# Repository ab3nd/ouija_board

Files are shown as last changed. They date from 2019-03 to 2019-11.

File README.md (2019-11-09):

# Ouija Board
Hardware and software plans for a ouija board that is controlled by a computer as an IO device. 

Now that this is public, I thought I ought to write up a bit more of a description of what we had hoped to do, what ended up making it into the puzzle, lessons learned, and so forth. 

The initial idea of the puzzle was that players would play some sort of word game with Spirits From Beyond. The players would enter letters by sliding the Ouija board planchette around the board, and the machinery under the board would answer back. Since the easy way to drive the planchette from under the board was a magnet, we looked at a couple of different approaches for figuring out where the magnet was on the board. 

One approach was to cover the underside of the board with magnetic field visualization film, and then look at it with a camera. This has two main drawbacks, one of them being that field visualization film is expensive, and the other is that the camera has to have enough space to see the underside of the board, an unobstructed view (so the machinery has to move out of the way), and good light. This is annoying set of constraints to deal with. 

Magnets can also be sensed with Hall Effect sensors. One idea was to put a grid of sensors under the board, and interpolate the location of the planchette from the readings of multiple sensors, another option was to just have a sensor under each letter. Having a sensor under each letter means you can lose the planchetette if it's moved to some place that isn't a letter. Having a grid of sensors of sufficient resolution to detect the planchette at any location would mean we blew the budget building a PCB the size of a Ouija board, and then yours truly went nuts hand-soldering a bunch of SOT-23 parts (or I guess we contaminate someone's oven stenciling and reflowing them). So we didn't do that. 

The final approach was that the head of the machine that moves the planchette also had a ring of sensors. When it was moving the planchette, it would raise a magnet to engage the planchette, and then move to drag the planchette around. When it was sensing user input, it would lower the magnet, so it was only sensing the planchette magnet, and then move to keep the field over the sensor ring balanced. Since it was counting steps that it made to keep the magnet centered, the system would know what letter the sensor ring was under. This approach kept the sensor PCB small, reduced the number of parts needed, and could track the planchette anywhere. 

But wait, you say. When the puzzle was in operation, the players would say the word they wanted to input, and the system would then spell it and do some wiggling between yes and no. There was no actual use of the planchette as an input device!

Using the planchette as an input device had a number of problems. One was that the system could lose the planchette due to users moving it too fast, or picking it up and putting it back down somewhere else. We could have fixed that by having the system sweep the board, but that leads into the second problem, which is that there was no feedback. If the user spelled "obliges", but were closer to the 'h' than the 'i' and the system saw "oblhges", the user wouldn't have a way to see that it hadn't picked up their input properly. If it lost the planchette and was doing a sweep to find it again, the user would have no idea what was going on, and the system would be ignoring their input. 

Also, when people are properly using a Ouija board to communicate with Spirits from Beyond, they say their questions, and the spirits answer by pushing the planchette around (or it's the ideomotor effect, or Joe (that jerk) always tries to make it spell "dongs"). Since we didn't have a good way to contact players of the Game who have passed Beyond the Veil, we used baby monitors in the room with each Ouija board, and a person listening to the baby monitor. The person was SSHed into the Raspberry PI that was running each board, and used a little script to drive the planchette around. That was why the boards sometimes spelled out things like "NATO", to try to get people to spell things out with the NATO phonetic alphabet, in cases where the word they said was unclear. So while the players were speaking to Spirits from Beyond, the spirits still had their mortal shells, and were Beyond the room divider, rather than the Veil of Death.

### Actual Implementation Information

The gantry that moved the planchette was a cheapo CNC device skellington from AliExpress, which uses an Arduino and a couple of stepper motor drivers. Two of the motors drive one axis, the other axis only has one motor. They had the somewhat weird design decision that the Arduino is powered over USB, while the stepper drivers and motors have their own, independent power supply. This makes some sense, since it means that A) the Arduino doesn't need to be protected from noise from the stepper motors, and B) the parts that would normally do A are not needed, so the whole thing is cheaper for the Chinese factory it came from. 

The Arduino was controlled over a serial-over-USB link from a Raspberry Pi running stock Raspbian. A little python script presented a user interface for a person connected to the Pi via SSH, and took care of stuff like Mastermind solving, because humans are made of fallible meat, and so cannot be trusted to do Mastermind in their heads at 2AM. 

The Python for the UI and Mastermind solving is in user_console.py and mastermind.py. The control code for the Arduino is in ouija_control.ino. They communicate using a pretty simple text-based protocol. The incomplete code for following the planchette is in sensor_track.ino. It results in some very jerky movement, and it would probably be better to do some form of vector representation of the magnet displacement and a PID loop to drive that to zero when the magnet is well-centered, as well as velocity control to have it operate smoothly, but that's Left As An Exercise For The Reader. 

### Hardware Notes

The sensors we used are AH49ENTR Hall effect sensors, SOT23-3 case size. We didn't do a lot of work to characterize sensors or anything, these are just what Ross happened to have on hand. He also had the 74hc4051 8ch analog demux that was used to communicate with the sensors. The sensor ring had 8 sensors, and the mux/demux has 8 channels, addressed with three address lines, so the total pin count going into the Arduino just fit what we had available after handling the stepper controllers, limit switches, and the servo to raise/lower the magnet. Of course, none of this got used in the final version except the limit switches. 

The limit switches allow the system to drive the planchette dragging magnet to a corner, and then count steps when moving the planchette to know where it is on the board. There are only one set of limit switches, the other end of each axis' travel is handled in software, by knowing how many steps it is to the other side of the board, and not taking steps that would move the head beyond that limit. 

The sense ring PCB design is in the sense_pcb folder in this repo. It was designed in Kicad, so between that, Python, etc. pretty much the whole thing except the servo control modules and the board they are on is open source. If you get the PCBs made, OSHPark will do a slightly more expensive job of it, while DirtyPCBs will do it cheaper and far slower. I've used both, they're both good. 

The CNC gantries that moved the magnet under the board were cut down from their orignal size. Aluminum is soft. If you want to cut it, it will smear like butter into hacksaws and abrasive wheels. The tool to use is just normal wood cutting implements, like miter saws and whatnot. 

Raspbian is pretty rough around the edges, I rant about it with a lot of swearing here:

http://gizmosmith.com/2019/08/28/raspbian-still-bad/

http://gizmosmith.com/2019/08/11/the-year-of-linux-on-the-desktop-is-ha-get-fucked/

### Measurements of Ouija board

Letters - 30mm tall by 14mm (I) - 38mm (W)

"NO" - 20mm tall by 35mm wide

"YES" - 20mm tall by 45mm wide

"GOOD BYE" - 20mm by 170mm wide

Closest approach to board edge - 25mm (bottom of "GOOD BYE")

Board thickness - 3.5mm

So the maximum radius of the sense ring is 25mm + 20mm/2 = 35mm, to be able to have the center of the actuated planchette window over the centerline of the letters closest to the edge of the board. 

The minimum diameter of the sense ring would be set by the size of the letters, and appears to be around 30-35mm, so a radius of 15-17mm. 

So the radius should be at minimum 15-17mm, and at maxium 35mm, bigger is easier to build (more PCB space), but 17mm can probably fit a ring. 

Active area is a box bounded by "YES/NO" at the top, "GOOD BYE" at the bottom, and the edges of the alphabet at the sides.
These measurements are from Sarah's board, which is the 1972 Parker/Berverly board, whereas those above are from my board, a 1960s Parker/Salem board. 

Width (outside of N to outside of Z) - 360mm
Height (top of YES/NO to bottom of GOODBYE) - 230mm

Board 295mm x 445mm (Conveniently, just inside the cutting area of my laser cutter)

These measurements are from my Ouija board, which is the older model. 

Width (outside of N to outside of Z) - 375mm
Height (top of YES/NO to bottom of GOODBYE) - 235mm

Board 295mm by 446mm

So the board size is essentially exactly the same, but the printing is a little different. The same size of plotter can work with either board, and the differences in text location can be handled by calibration. 

### Some CNC Devices to Use

A4 paper size is 210 mm × 297 mm (8.27 in × 11.7 in), so the plotters with an A4-sized area are a little too small for a traditional Ouija board. 
A3 paper is 297 mm × 420 mm (11.69 in × 16.54 in), so an A3 plotter would work. 

https://www.aliexpress.com/item/DIY-XY-Plotter-drawbot-pen-drawing-robot-machine-lettering-corexy-A4-A3-engraving-area-frame-plotter/32952725307.html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,searchweb201602_6_10065_10130_10068_10890_10547_319_10546_317_10548_10545_10696_453_10084_454_10083_10618_10307_537_536_10902_10059_10884_10887_321_322_10103,searchweb201603_16,ppcSwitch_0&algo_expid=b5854729-7ad1-4867-a162-900024d3b36f-2&algo_pvid=b5854729-7ad1-4867-a162-900024d3b36f

https://www.aliexpress.com/item/50-X-65cm-Laser-Engraving-Machine-Wood-Router-CNC-DIY-Laser-Engraver-Machine-For-Desktop-Cutting/32970303676.html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,searchweb201602_6_10065_10130_10068_10890_10547_319_10546_317_10548_10545_10696_453_10084_454_10083_10618_10307_537_536_10902_10059_10884_10887_321_322_10103,searchweb201603_16,ppcSwitch_0&algo_expid=b95455ae-6d0d-4979-8a5e-edf8464dbc0f-14&algo_pvid=b95455ae-6d0d-4979-8a5e-edf8464dbc0f

Second one is huge, could be cut down to fit under board. Very tall, though. 

### Magnet Grip

We replaced the planchette window/pointer with a cut piece of acrylic with a neodymium magnet in it, 5mm is about the max diameter for the magnet to still have it look good.

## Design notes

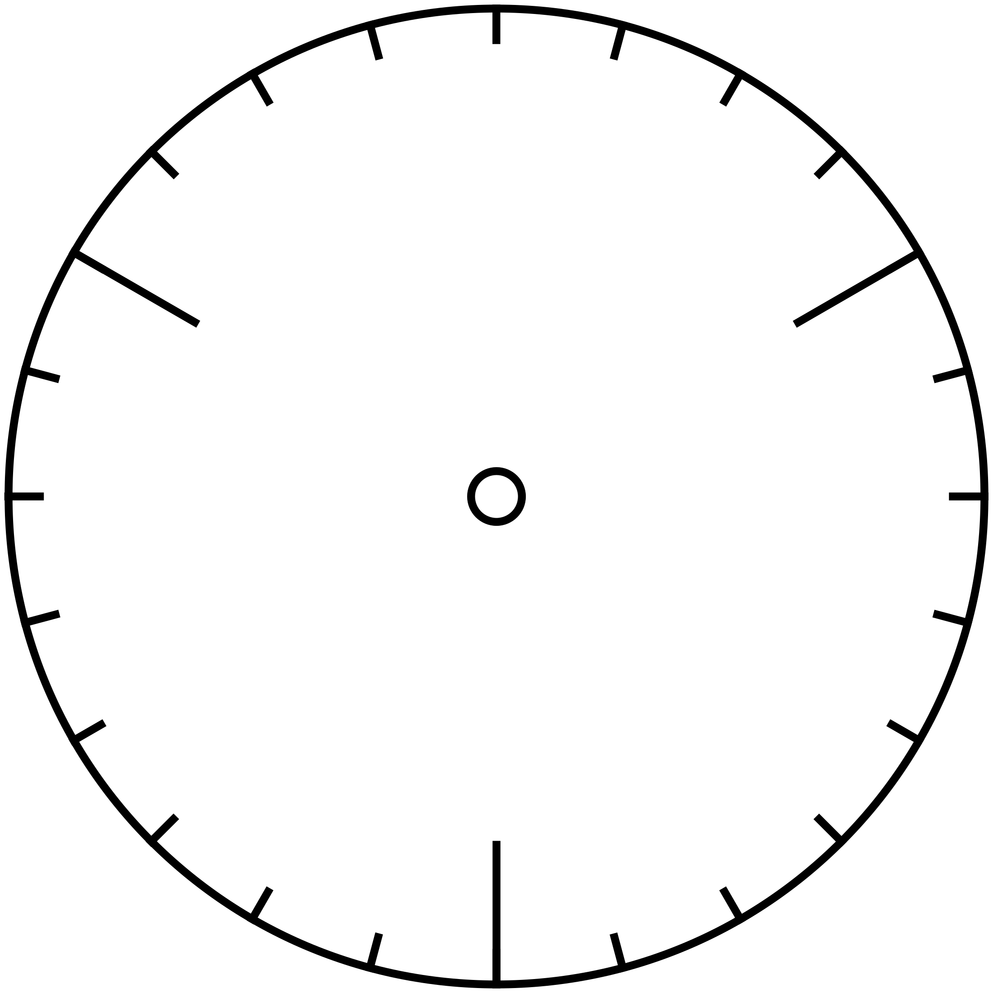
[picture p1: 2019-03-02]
graphics/layout.svg.png

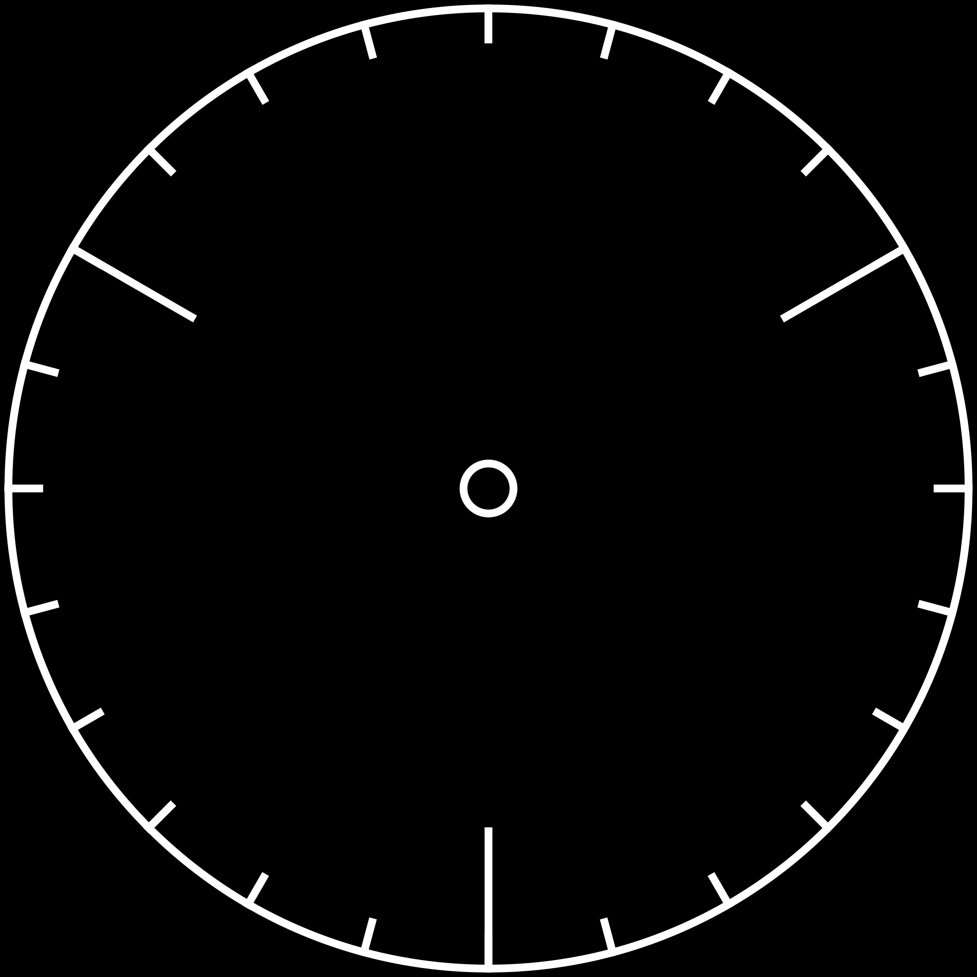
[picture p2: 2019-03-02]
graphics/layout.invert.png

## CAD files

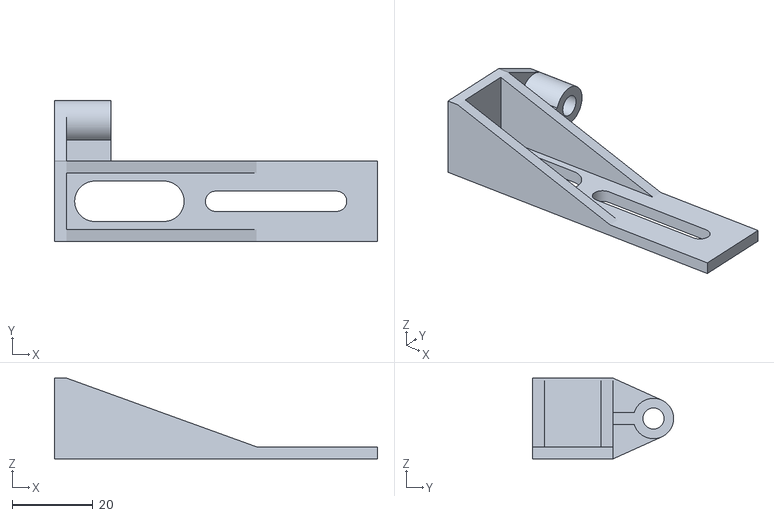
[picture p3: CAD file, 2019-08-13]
hardware/basic_magnet_holder.stl
80.0 x 35.0 x 20.0

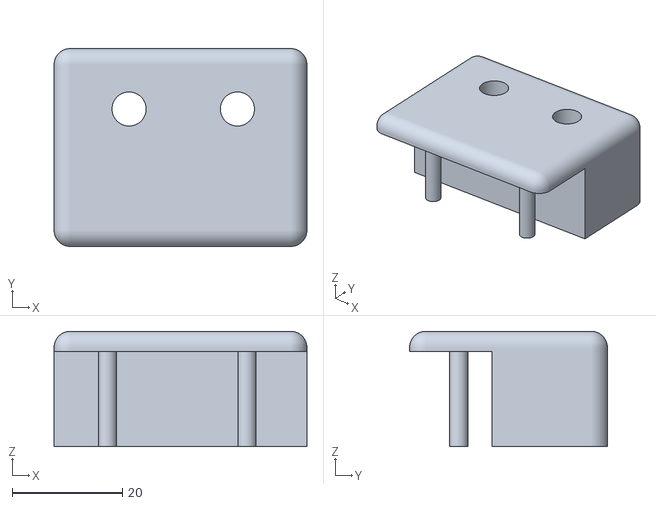
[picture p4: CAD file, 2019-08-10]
hardware/microswitch_mount.stl
46.0 x 36.0 x 21.0

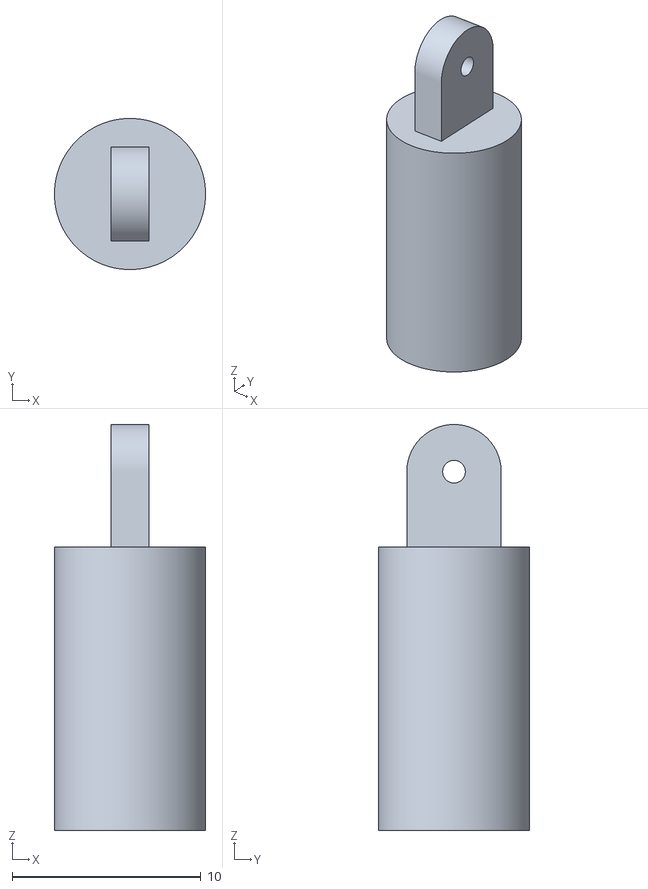
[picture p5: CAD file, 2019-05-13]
hardware/magnet_holder.stl
8.00 x 8.00 x 21.5

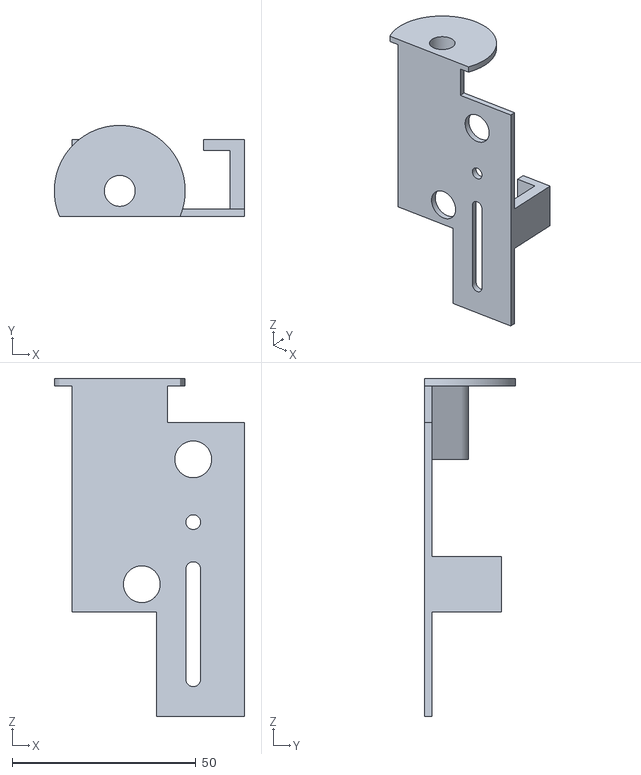
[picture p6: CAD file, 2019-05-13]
hardware/pcb_holder.stl
51.8 x 24.8 x 92.0

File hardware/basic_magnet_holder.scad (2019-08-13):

$fn=60;

module mount_surface(){
    difference(){
        union(){
            angle_length = 50;
            angle_height = 20;
            thickness = 3;
            //Flanges on the sides
            hull(){
                translate([0, 7, 0]){
                    cube([angle_length, thickness, thickness]);
                    cube([thickness, thickness, angle_height]);
                }
            }
            hull(){
                translate([0,-10, 0]){
                    cube([angle_length, thickness, thickness]);
                    cube([thickness, thickness, angle_height]);
                }
            }
            
            //Mount panel
            translate([0,-10,0]){
                cube([80,20,thickness]);
            }
            
            //Magnet
            translate([0,20,10]){
                rotate([0, 90, 0]){
                    difference(){
                        cylinder(r=5, h=14);

                    }
                }
            }
            

            
            //Rectangle connector
            translate([0,10,8.5]){
                cube([14,7,3]);
            }
            
            //Flat end connector
            hull(){
                translate([0,20,10]){
                    rotate([0, 90, 0]){
                        cylinder(r=5, h=3);
                    }
                }
                translate([0,-10, 0]){
                    cube([3, 20, angle_height]);
                }
            }
        }
        
        
        // Cutouts for mounting
        union(){
            translate([0,0,-1]){
                translate([10, 0, 0]){
                    cylinder(h=8, r=5);
                }
                
                translate([25.1+2, 0, 0]){
                    cylinder(h=8, r=5);
                }
                   
                translate([10,-5, 0]){
                    cube([17,10,8]);
                }

                translate([25.1+4+10.78, 0, 0]){
                    cylinder(h=8, r=2.5);
                    translate([0,-2.5, 0]){
                        cube([30,5,8]);
                    }
                }
                
                translate([25.1+4+10.78 +30, 0, 0]){
                    cylinder(h=8, r=2.5);
                }
            }

            //Magnet hole
            translate([0,20,10]){
                rotate([0, 90, 0]){
                    translate([0,0,-0.5]){
                        cylinder(r=2.62, h=15);
                    }
                }
            }               
         }
      }
  }




mount_surface();

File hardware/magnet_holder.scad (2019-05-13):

module magnet_holder(){
   //Body with hole
   difference(){
      cylinder(r=4, h=15, $fn=200);
      translate([0,0,-3]){
         cylinder(r=2.6, h=15, $fn=200);
      }
   }

   //Tab with a hole in it
   difference(){
      union(){
         translate([-2.5, 0, 19]){
            translate([1.5, 0, 0]){
               rotate([0,90,0]){
                  cylinder(r=2.5, h=2, $fn=200);
               }
            }
         }

         translate([0,0,17]){
               cube([2,5,4], center=true);
         }
      }

      translate([-2.5, 0, 19]){
         rotate([0,90,0]){
            cylinder(r=0.6, h=5, $fn=200);
         }
      }
   }
}

magnet_holder();

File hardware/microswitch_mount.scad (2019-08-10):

$fn = 60;

module microswitch(){
    sw_hole_d = 3.3;
    sw_hole_r = sw_hole_d/2;
    sw_hole_h = 4 + sw_hole_r+0.4;
    sw_hole_offset = 9.7 + sw_hole_r+0.4;
    sw_hole_sep = 25.35;

    difference(){
        //Body of the microwitch
        color("grey"){
            cube([49.2, 17.3, 20.9]);
        }

        //Mount holes
        translate([sw_hole_offset, -1, sw_hole_h]){ 
            rotate([-90,0,0]){
                cylinder(r = sw_hole_r, h = 25);
                translate([sw_hole_sep, 0, 0]){
                    cylinder(r=sw_hole_r, h = 25);
                }
            }
        }
    }
}

module holder(){
    difference(){
        translate([5, -12, 0]){ 
            color("blue"){
                minkowski(){
                    cube([40, 30, 18]);
                    sphere(r=3);
                }
            }
        }
        
        //measured from the strut
        groove_w = 6.2;
        translate([25.5, 10, -10]){
            translate([(13.5+groove_w)/2, 0, 0]){
                cylinder(r=groove_w/2, h = 40);
            }
            translate([-(13.5+groove_w)/2, 0, 0]){
                cylinder(r=groove_w/2, h = 40);
           }
        }
        
        //Delete the bottom face
        translate([0,-20,-7.9999]){
            cube([50, 50, 8]);
        }
    }
}

difference(){
    holder();
    rotate([90, 0, 0]){
        microswitch();
    }
}

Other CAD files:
hardware/pcb_holder.scad

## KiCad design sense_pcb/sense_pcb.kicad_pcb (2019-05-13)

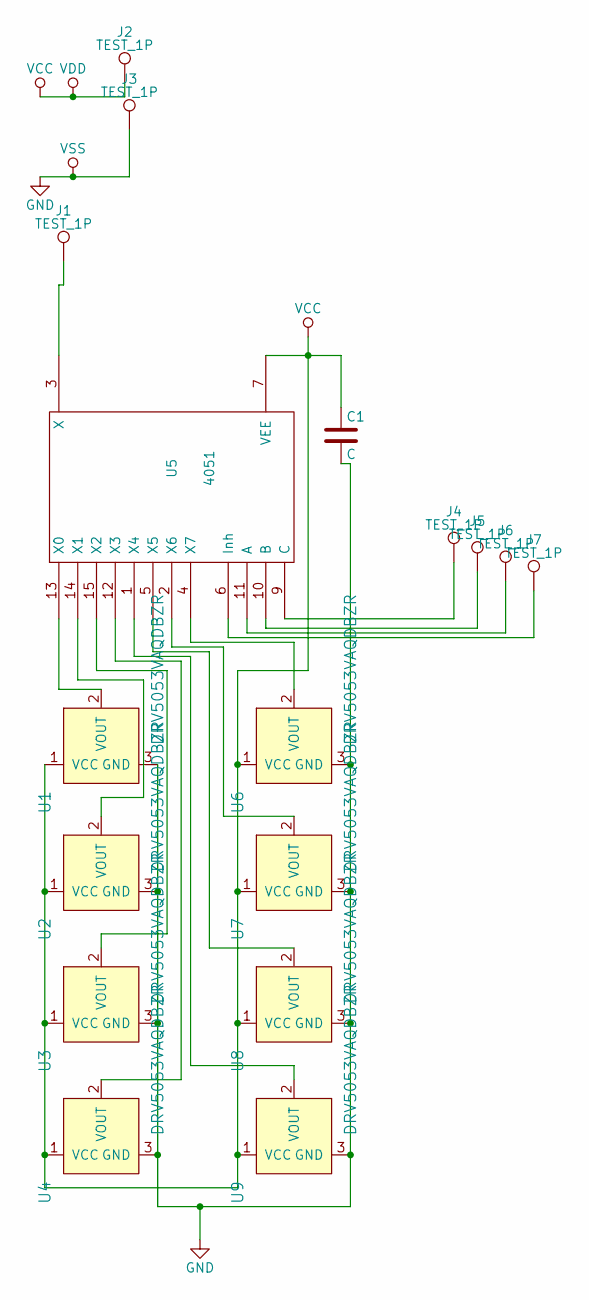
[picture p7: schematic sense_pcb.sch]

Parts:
C1: C; C_1206_HandSoldering
J1, J2, J3, J4, J5, J6, J7: TEST_1P; Measurement_Point_Round-SMD-Pad_Small
U1, U2, U3, U4, U6, U7, U8, U9: DRV5053VAQDBZR; SOT-23-3; MPN DRV5053VAQDBZR; Digi-Key_PN 296-38460-1-ND
U5: 4051; SO-16-N

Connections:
GND: C1.2, J3.1, U1.3 (GND), U2.3 (GND), U3.3 (GND), U4.3 (GND), U5.8 (VSS), U6.3 (GND), U7.3 (GND), U8.3 (GND), U9.3 (GND)
unnamed: J1.1, U5.3 (X)
unnamed: J4.1, U5.9 (C)
unnamed: J5.1, U5.10 (B)
unnamed: J6.1, U5.11 (A)
unnamed: J7.1, U5.6 (Inh)
unnamed: U1.2 (VOUT), U5.13 (X0)
unnamed: U2.2 (VOUT), U5.14 (X1)
unnamed: U3.2 (VOUT), U5.15 (X2)
unnamed: U4.2 (VOUT), U5.12 (X3)
unnamed: U5.1 (X4), U9.2 (VOUT)
unnamed: U5.2 (X6), U7.2 (VOUT)
unnamed: U5.4 (X7), U6.2 (VOUT)
unnamed: U5.5 (X5), U8.2 (VOUT)
VCC: C1.1, J2.1, U1.1 (VCC), U2.1 (VCC), U3.1 (VCC), U4.1 (VCC), U5.7 (VEE), U5.16 (VDD), U6.1 (VCC), U7.1 (VCC), U8.1 (VCC), U9.1 (VCC)

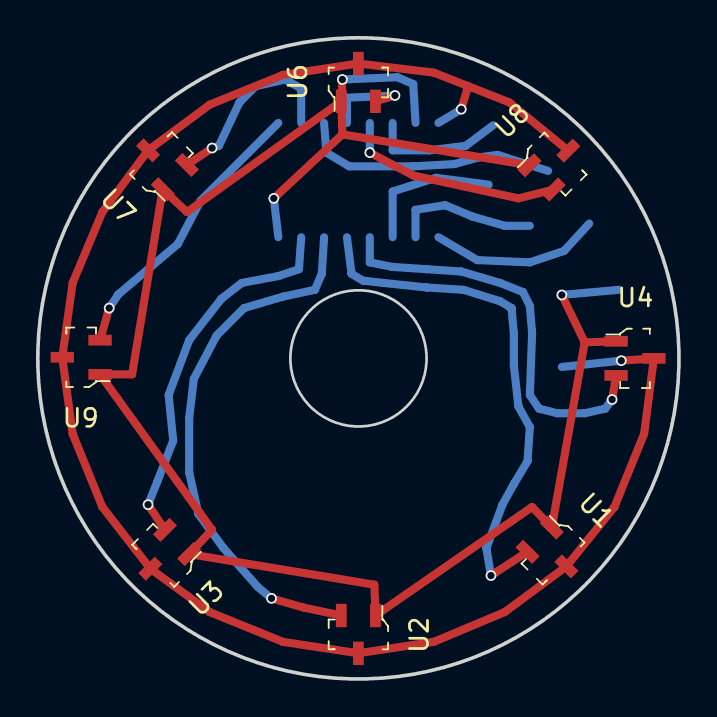
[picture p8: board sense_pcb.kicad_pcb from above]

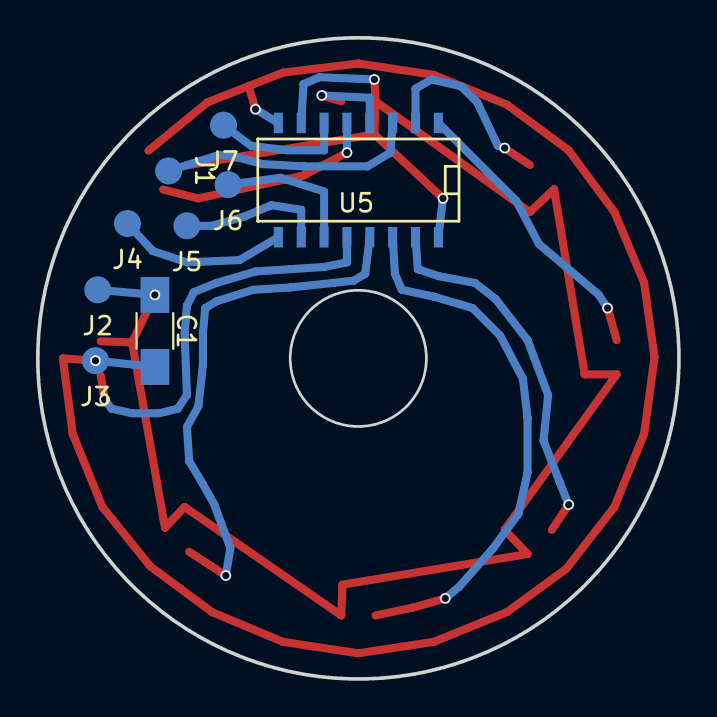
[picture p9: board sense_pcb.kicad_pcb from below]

Board: 2 copper layers, 35.6 x 35.6 mm, 17 parts (9 on the bottom side), 15 nets.

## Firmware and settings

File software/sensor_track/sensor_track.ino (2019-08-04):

/* Control software for the Ouija Board. The board is an Arduino Nano with the old bootloader.
   By Ab3nd.
*/

#include <Servo.h>

//Limit switch connections
#define LIMIT_X 9
#define LIMIT_Y 10

//Stepper control
#define ENABLE 8
#define DIR_X 5
#define DIR_Y 6
#define STEP_X 2
#define STEP_Y 3

//Sensor
#define ENABLE_SENSE 4
#define S0 7
#define S1 11
#define S2 12
#define SENSE A0

#define SERVO_PIN 13

//Measurements, from home, of the working area, in steps
#define Y_MAX 30921
#define X_MAX 18995

/* "NO"   600   5500
   "YES"  600   24600
   A      8800  29000
   B      7200  26500
   C      6500  24000
   D      5500  22000
   E      5200  20000
   F      5100  17500
   G      5000  15500
   H      5000  13500
   I      5000  11000
   J      5500  9000
   K      6000  7000
   L      6800  4500
   M      8300  2300
   N      13200 28300
   O      11600 26400
   P      10600 24400
   Q      9600  22400
   R      8800  20200
   S      8600  17700
   T      8400  15700
   U      8100  13500
   V      8300  11000
   W      9000  8500
   X      10500 6100
   Y      11500 4000
   Z      12800 1800
*/
int current_x = 0;
int current_y = 0;

struct point {
  int x;
  int y;
};

//26 letters, in order a-z
struct point letters[26] = {
  {8800, 29000},
  {7200, 26500},
  {6500, 24000},
  {5500, 22000},
  {5200, 20000},
  {5100, 17500},
  {5000, 15500},
  {5000, 13500},
  {5000, 11000},
  {5500, 9000},
  {6000, 7000},
  {6800, 4500},
  {8300, 2300},
  {13200, 28300},
  {11600, 26400},
  {10600, 24400},
  {9600, 22400},
  {8800, 20200},
  {8600, 17700},
  {8400, 15700},
  {8100, 13500},
  {8300, 11000},
  {9000, 8500},
  {10500, 6100},
  {11500, 4000},
  {12800, 1800}
};

point no = {600, 5500};
point yes = {600, 24600};

int readings[8] = {0, 0, 0, 0, 0, 0, 0, 0};
int cal_readings[8] = {0, 0, 0, 0, 0, 0, 0, 0};

/* Map counts on the address lines of the mux to indices for readings
   so that the readings are sequential around the ring */
int addr_map[8] = {0, 1, 2, 7, 3, 6, 4, 5};

Servo mag_lift;

String serial_cmd;
String guess;

//The time in millis the system last moved
unsigned long last_moved;

//The last character the system sent
char last_sent;

bool sent_answer;
bool sent_msg;

void setup() {

  //Set up the magnet height
  mag_lift.attach(SERVO_PIN);
  //90 is very low, 40 looks about good
  mag_lift.write(40);

  //Limit switches
  pinMode(LIMIT_X, INPUT);
  pinMode(LIMIT_Y, INPUT);

  //Set up the stepper control
  pinMode(ENABLE, OUTPUT);
  pinMode(DIR_X, OUTPUT);
  pinMode(DIR_Y, OUTPUT);
  pinMode(STEP_X, OUTPUT);
  pinMode(STEP_Y, OUTPUT);

  // Hall ring sensor
  pinMode(ENABLE_SENSE, OUTPUT);
  pinMode(S0, OUTPUT);
  pinMode(S1, OUTPUT);
  pinMode(S2, OUTPUT);
  pinMode(SENSE, INPUT);

  // Set up sensor
  digitalWrite(ENABLE_SENSE, HIGH);
  digitalWrite(S0, LOW);
  digitalWrite(S1, LOW);
  digitalWrite(S2, LOW);

  //Accumulate 10 samples
  for (int count = 0; count < 10; count++) {
    for (byte ii = 0; ii < 8; ii++)
    {
      //Disable the switch
      digitalWrite(ENABLE_SENSE, HIGH);
      //Set the address bits
      (ii & B00000001) ? digitalWrite(S0, HIGH) : digitalWrite(S0, LOW);
      (ii & B00000010) ? digitalWrite(S1, HIGH) : digitalWrite(S1, LOW);
      (ii & B00000100) ? digitalWrite(S2, HIGH) : digitalWrite(S2, LOW);
      digitalWrite(ENABLE_SENSE, LOW);
      cal_readings[addr_map[ii]] += analogRead(SENSE);
    }
  }

  //Get their average
  for (int idx = 0; idx < 8; idx++)
  {
    //Each reading should be around 512 with no magnet, so these
    //should all be around 5120, and so not have an underflow
    //dividing by 10
    cal_readings[idx] = cal_readings[idx] / 10;
  }

  //For debugging
  Serial.begin(9600);

  //Just for initialization
  last_moved = millis();
}


void move_home() {
  //Enable stepper drivers
  digitalWrite(ENABLE, LOW);

  //Home x axis first
  digitalWrite(DIR_X, LOW);
  digitalWrite(STEP_X, LOW);
  while (digitalRead(LIMIT_X) == 1) {
    digitalWrite(STEP_X, HIGH);
    delayMicroseconds(200);
    digitalWrite(STEP_X, LOW);
    delayMicroseconds(200);
  }

  //Home Y axis, it uses opposite DIR_Y setting
  digitalWrite(DIR_Y, HIGH);
  digitalWrite(STEP_Y, LOW);
  while (digitalRead(LIMIT_Y) == 1) {
    digitalWrite(STEP_Y, HIGH);
    delayMicroseconds(200);
    digitalWrite(STEP_Y, LOW);
    delayMicroseconds(200);
  }

  //Disable stepper drivers
  digitalWrite(ENABLE, HIGH);

  //Reset the position counters
  current_x = current_y = 0;
}

void single_step(int dir, int axis, int vel) {

  // Enable axis and maintain step counts
  digitalWrite(ENABLE, LOW);
  if (axis == STEP_X) {
    digitalWrite(DIR_X, dir);
    //High is away from home for X
    if (dir) {
      current_x++;
    }
    else {
      current_x--;
    }
  }
  else {
    digitalWrite(DIR_Y, dir);
    //HIGH is towards home for Y
    if (dir) {
      current_y--;
    }
    else {
      current_y++;
    }
  }

  // Single step
  digitalWrite(axis, HIGH);
  delayMicroseconds(vel);
  digitalWrite(axis, LOW);
  delayMicroseconds(vel);

  //Update last move
  last_moved = millis();
}

void move_to(int x, int y, int vel) {
  //In this house, we only move within the operating area of the gantry
  y = constrain(y, 0, Y_MAX);
  x = constrain(x, 0, X_MAX);

  //Figure out X and Y directions
  int x_dir = HIGH;  // Away from home
  if ((current_x - x) > 0) {
    x_dir = LOW;  // Towards home
  }

  int y_dir = LOW;  //Away from home
  if ((current_y - y) > 0) {
    y_dir = HIGH;  // Towards home
  }

  //Ratio of X to Y, so how many steps to take of each per cycle
  float ratio = float(abs(current_x - x)) / float(abs(current_y - y));

  int stepX, stepY;
  if (ratio >= 1) {
    stepX = int(ratio);
    stepY = 1;
  } else {
    stepX = 1;
    stepY = int(1.0 / ratio);
  }

  while ((current_y != y) && (current_x != x)) {
    //Do the x steps, if any
    for (int ii = 0; ii < stepX; ii++) {
      if (current_x == x) {
        break;
      }
      single_step(x_dir, STEP_X, vel);
    }
    //Do the y steps, if any
    for (int ii = 0; ii < stepY; ii++) {
      if (current_y == y) {
        break;
      }
      single_step(y_dir, STEP_Y, vel);
    }
  }

  while (current_y != y) {
    single_step(y_dir, STEP_Y, vel);
  }

  while (current_x != x) {
    single_step(x_dir, STEP_X, vel);
  }
}

void say_string(String msg) {
  int index = 0;
  struct point p;
  //For all the letters
  for (int ii = 0; ii < msg.length(); ii++) {
    //String is all lowercase, so subtracting 'a' converts from ascii
    //to a=0, b=1, c=2,..., which can then be used to
    //look up coordinates in a lookup table and move
    index = msg[ii] - 'a';
    p = letters[index];
    move_to(p.x, p.y, 100);
    //Delay to let people read it off
    delay(1000);
    //If the next letter is the same as this letter
    while ((ii != msg.length() - 1) && (msg[ii] == msg[ii + 1])) {
      //Skip the next letter
      ii++;
      //move off this letter and then back on
      move_to(current_x - 800, current_y - 800, 100);
      move_to(current_x + 800, current_y + 800, 100);
      delay(1000);
    }
  }
}

void update_sensor() {
  for (byte ii = 0; ii < 8; ii++)
  {
    //Disable the switch
    digitalWrite(ENABLE_SENSE, HIGH);
    //Set the address bits
    (ii & B00000001) ? digitalWrite(S0, HIGH) : digitalWrite(S0, LOW);
    (ii & B00000010) ? digitalWrite(S1, HIGH) : digitalWrite(S1, LOW);
    (ii & B00000100) ? digitalWrite(S2, HIGH) : digitalWrite(S2, LOW);
    digitalWrite(ENABLE_SENSE, LOW);
    readings[addr_map[ii]] = analogRead(SENSE) - cal_readings[addr_map[ii]];
  }
}

bool close_to(int a, int b, int thresh) {
  return b - thresh <= a <= b + thresh;
}

float distance(point p1, point p2) {
  return sqrt(pow(p1.x - p2.x, 2) + pow(p1.y - p2.y, 2));
}

char closest_letter() {
  //Hacky, but the biggest distance between two points on the
  //board can't be more than the sum of the edges of the board
  unsigned long min_dist = X_MAX + Y_MAX;
  int min_idx = 0;
  float d = 0;
  point current = {current_x, current_y};
  for (int ii = 0; ii < 25; ii++) {
    d = distance(current, letters[ii]);
    if (d < min_dist)
    {
      min_idx = ii;
      min_dist = d;
    }
  }

  //Capital A is 65;
  char retval = (char)(min_idx + 65);

  //Check if the distance to "No" is even closer
  d = distance(no, current);
  if (d < min_dist) {
    retval = 0;
    min_dist = d;
  }
  
  //Finally, check if the distance to "Yes" is closer
  d = distance(yes, current);
  if (d < min_dist) {
    retval = 1;
    min_dist = d;
  }

  //Too far from any letter to count
  if(min_dist > 2000)
  {
    retval = 2;
  }

  //Return is a char, but it's 0 for No, 1 for Yes, 2 for no letter, and the letter for A-Z
  return retval;
}

void follow_planchette() {
  int vel = 100;
  int move_thresh = 10;

  //Get the maximum sensor reading
  byte max_idx = 0;
  int max_val = 0;
  for (byte ii = 0; ii < 8; ii++)
  {
    if (readings[ii] > max_val)
    {
      max_val = readings[ii];
      max_idx = ii;
    }
  }

  //If we need to get moving
  if (max_val > move_thresh) {
    //Get the second max
    byte second_max_idx = 0;
    byte second_max = 0;

    if (max_idx == 0)
    {
      //Handle wrap at zero
      (readings[max_idx + 1] > readings[7]) ? second_max_idx = max_idx + 1 : second_max_idx = 7;
    }
    else if (max_idx == 7)
    {
      //Handle wrap at 7
      (readings[0] > readings[max_idx - 1]) ? second_max_idx = 0 : second_max_idx = max_idx - 1;
    }
    else
    {
      //Check sensors next to this sensor
      (readings[max_idx + 1] > readings[max_idx - 1]) ? second_max_idx = max_idx + 1 : second_max_idx = max_idx - 1;
    }

    //Figure out the move
    int move_dist = 15 * max_val; //was 200
    int target_x = current_x;
    int target_y = current_y;

    //Add a little bit to current postion to get new position
    if ((max_idx == 0 && second_max_idx == 1) || (max_idx == 1 && second_max_idx == 0))
    {
      //Down and Left
      target_x += move_dist;
      target_y += move_dist;
    }
    else if ((max_idx == 1 && second_max_idx == 2) || (max_idx == 2 && second_max_idx == 1))
    {
      //Left
      target_y += move_dist;
    }
    else if ((max_idx == 2 && second_max_idx == 3) || (max_idx == 3 && second_max_idx == 2))
    {
      //Up and Left
      target_x -= move_dist;
      target_y += move_dist;
    }
    else if ((max_idx == 3 && second_max_idx == 4) || (max_idx == 4 && second_max_idx == 3))
    {
      //Up
      target_x -= move_dist;
    }
    else if ((max_idx == 4 && second_max_idx == 5) || (max_idx == 5 && second_max_idx == 4))
    {
      //Up and Right
      target_x -= move_dist;
      target_y -= move_dist;
    }
    else if ((max_idx == 5 && second_max_idx == 6) || (max_idx == 6 && second_max_idx == 5))
    {
      //Right
      target_y -= move_dist;
    }
    else if ((max_idx == 6 && second_max_idx == 7) || (max_idx == 7 && second_max_idx == 6))
    {
      //Down and Right
      target_x += move_dist;
      target_y -= move_dist;
    }
    else if ((max_idx == 7 && second_max_idx == 0) || (max_idx == 0 && second_max_idx == 7))
    {
      //Down
      target_x += move_dist;
    }

    move_to(target_x, target_y, vel);
  }
}

void move_yes() 
{
  if ((current_y == 24600) && (current_x == 600)) {
    //move off and then back on
    move_to(current_x - 500, current_y - 800, 100);
    move_to(current_x + 500, current_y + 800, 100);
  }
  else {
    move_to(600, 24600, 100);
  }  
}

void move_no()
{
  if ((current_y == 5500) && (current_x == 600)) {
    //move off and then back on
    move_to(current_x - 500, current_y - 800, 100);
    move_to(current_x + 500, current_y + 800, 100);
  }
  else {
    move_to(600, 5500, 100);
  }  
}

bool get_serial_cmd() {
  Serial.println("get_serial_cmd called");
  
  while (!Serial.available()) {} // wait for data to arrive

  int index = 0;
  
  if (Serial.available()) {
    serial_cmd = Serial.readStringUntil('\n');
    //Previous line would block until we got something
    //The returning command from the user is a string to say,
    //And then a yes/no answer string
    if (serial_cmd.startsWith("s")) {

      //Split on first space, command is of the form "s some string here"
      index = serial_cmd.indexOf(" ");
      String message = serial_cmd.substring(index + 1);
      //Send it back as confirmation
      say_string(message);

      sent_msg = true;
    }
    else if (serial_cmd.startsWith("a")) {
      //Answer, message is of the form "a yyny" or similar 
      index = serial_cmd.indexOf(" ");
      String answer = serial_cmd.substring(index + 1);
      for(int ii = 0; ii < answer.length(); ii++)
      {
        if(answer.charAt(ii) == 'y')
        {
          move_yes();
        }
        else if(answer.charAt(ii) == 'n')
        {
          move_no();
        }
      }
      sent_answer = true;
    }

    //only return true if both are true
    return sent_answer && sent_msg;
  }
}

enum states {START, FOLLOW_MOVE, SEND_CHAR, DONE_WAIT};
uint8_t state = START;

void loop() {
  update_sensor();
  run_state_machine();
}

void run_state_machine()
{
  switch (state)
  {
    case DONE_WAIT:
      //Only returns true if both the answer and the message have both been sent
      //otherwise, we stay in this state
      if(get_serial_cmd())
      {
        //Reset what was sent
        sent_answer = false;
        sent_msg = false;
        state = FOLLOW_MOVE;
      }
      break;
    case START:
      //Home the axes
      move_home();
      state = FOLLOW_MOVE;
      guess = "";
      break;
    case FOLLOW_MOVE:
      follow_planchette();
      if ((millis() - last_moved) > 1500)
      {
        state = SEND_CHAR;
      }
      break;
    case SEND_CHAR:
      //Get the closest character
      char toSend = closest_letter();
      if (toSend == 1) //"Yes"
      {
        //If it is "yes", send the accumulated string
        Serial.println(guess);
        guess = "";
        state = DONE_WAIT;
      }
      else if (toSend == 2) // No character
      {
        //Just update last sent character
        last_sent = toSend;
        //Keep accumulating letters
        state = FOLLOW_MOVE;
      }
      else if (toSend >= 65 && toSend <= (65+26)) //A letter 
      {
        //Dedupe characters, add it to the string exactly once
        if(toSend != last_sent){
          guess.concat(toSend);
          last_sent = toSend;
        }
        //Keep accumulating letters
        state = FOLLOW_MOVE;
      }
      else
      {
        //We don't handle "no" yet, other cases as well...
        state = FOLLOW_MOVE;
        last_sent = toSend;
      }
      break;
  }
}

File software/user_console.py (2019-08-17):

import cmd
import re
import sys
import serial
from serial.tools import list_ports
from mastermind import check_word


class OuijaShell(cmd.Cmd):
    intro = 'Welcome to the great beyond.  Type help or ? to list commands.\n'
    prompt = '(spook) '
    
    # ----- basic commands -----
    def do_move(self, arg):
        'Move to a location: move x y'
        args = parse(arg)
        if len(args) == 2:
            self.serial_port.write(b"m {0} {1}\n".format(args[0], args[1]))
        else:
            print "Move takes two args, x and y"
            return False
        line = self.serial_port.readline()
        print line
        
    def do_say(self, arg):
        'Spell out a phrase: say Some phrase here...'
        #Cut the string down to all lowercase no punctuation
        letters = re.sub("[^A-Za-z]*", "", arg).lower()
        self.serial_port.write(b"s {0}\n".format(letters))
        line = self.serial_port.readline()
        print line
        
    def do_home(self, arg):
        'Home the control head: home'
        self.serial_port.write(b"h\n")
        line = self.serial_port.readline()
        print line

    def do_yes(self, arg):
        'Move to the "yes" message'
        self.serial_port.write(b"y\n")
        line = self.serial_port.readline()
        print line

    def do_intro(self, arg):
        self.serial_port.write(b"s {0}\n".format("saysevenletterword"))
        line = self.serial_port.readline()
        print line

    def do_no(self, arg):
        'Move to the "no" message'
        self.serial_port.write(b"n\n")
        line = self.serial_port.readline()
        print line

    def do_check(self, arg):
        'Checks a word, which spells the word out and then outputs yes/no code mastermind style: check [target word] [their guess]'
        word, guess = arg.split(" ")
        word = re.sub("[^A-Za-z]*", "", word).lower()
        guess = re.sub("[^A-Za-z]*", "", guess).lower()
        self.serial_port.write(b"s {0}\n".format(guess))
        # Just doing this so it blocks
        line = self.serial_port.readline()
        # TODO make sure the dict is in 
        score = check_word(word, guess)
        for point in score:
            if point == 'y':
                self.serial_port.write(b"y\n")
            else:
                self.serial_port.write(b"n\n")
            #Block until it's done
            line = self.serial_port.readline()
        #Move to the "Ouija" logo
        self.serial_port.write(b"m {0} {1}\n".format(2000, 14500))
        #Block until it's done
        line = self.serial_port.readline()
            
            #TODO if you want a delay, put it here
        
    def do_quit(self, arg):
        'Shut everything down and stop: quit'
        print('The spirits have said enough')
        return True

    def preloop(self):
        #Find the serial ports
        ports = list_ports.grep("ttyUSB")
        try:
            #Get the first port, or fail if there are none
            port = ports.next()
            self.serial_port = serial.Serial()
            self.serial_port.baudrate = 9600
            self.serial_port.port = port.device
            self.serial_port.timeout = 30
            self.serial_port.open()
            if not self.serial_port.is_open:
                print "Could not open serial port {0}".format(port.device)
                return True
        except StopIteration:
            print "No serial ports found"
            return True

def parse(arg):
    'Convert a series of zero or more numbers to an argument tuple'
    return tuple(map(int, arg.split()))

if __name__ == '__main__':
    OuijaShell().cmdloop()

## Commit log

2019-03-02 adds sense pcb schematic
    [sense_pcb.kicad_pcb, sense_pcb.sch]
2019-03-02 adds component footprints
    [_saved_sense_pcb.sch]
2019-03-02 adds netlist and pcb
    [_saved_sense_pcb.sch, sense_pcb.kicad_pcb]
2019-03-02 adds measurements
    [_saved_sense_pcb.sch]
2019-03-02 adds 35mm layout for parts
2019-03-02 IC layout done
    [_saved_sense_pcb.sch, sense_pcb.kicad_pcb, sense_pcb.sch]
2019-03-02 much smaller pads
    [sense_pcb.kicad_pcb]
2019-03-11 removed 2/3 of the sensors from the schematic to shrink it
    [sense_pcb.sch]
2019-03-11 went over to Kicad 5.0, seems legit so far
    [sense_pcb.kicad_pcb, sense_pcb.sch]
2019-03-11 layout with 8 sensors, no routing yet
    [sense_pcb.kicad_pcb]
2019-03-11 routing complete
    [sense_pcb.kicad_pcb]
2019-03-11 adds v1 manufacturing files as sent to dirtypcbs.com
    [sense_pcb.kicad_pcb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]
2019-03-30 basic control of the steppers
2019-04-02 adds draft hardware for mounting magnet, servo, sense pcb
    [magnet_holder.stl, pcb_holder.scad, pcb_holder.stl]
2019-04-28 adds sensor test
    [sense_pcb.kicad_pcb]
2019-04-28 sensor test program works, there is a bug in the PCB (Vee -> gnd, not v+)
    [sensor_test.ino]
2019-05-02 new version pcb holder
    [pcb_holder.scad, pcb_holder.stl]
2019-05-02 Magnet holder in seperate file
    [magnet_holder.scad, magnet_holder.stl]
2019-05-05 redesign of pcb holder
    [magnet_holder.scad, magnet_holder.stl, pcb_holder.scad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]
2019-05-13 updated pcb from laptop
    [sense_pcb.kicad_pcb]
2019-05-19 new limit test, servo for magnet
2019-07-29 adds first cut at sensor tracking
2019-08-03 following, sends characters, needs de-duplication on the other end
2019-08-04 multiple loops of execution worked, servo still has issues
    [sensor_track.ino]
2019-08-10 adds files for switch mounts
    [microswitch_mount.scad, microswitch_mount.stl]
2019-08-10 adds mastermind checker
    [microswitch_mount.stl]
2019-08-13 adds basic magnet holder
    [basic_magnet_holder.scad, basic_magnet_holder.stl]
2019-08-17 switched sense of answer command
